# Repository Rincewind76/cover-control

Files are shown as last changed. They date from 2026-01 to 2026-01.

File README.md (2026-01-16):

# Starting Setup
I have the following equipment:
* WandererCover V4-EC Professional Flatpanel
* Celestron EdgeHD 800 with 0.7 reducer and Off-Axis-Guide and a Dew Heater
* ASIAir Plus
* ZWO ASI585MC (main) and ZWO ASI220M (Guide)
* ZWO Autofocuser
* ZWO Filter Wheel
* Sky Watcher EQ6-R Pro

So all equipment can be conviniently controlled by the ASIAir Plus, except the Wanderer Cover...
(To be fair: The Cover can be controlled by a series of power on/off cycles via the ASIAir - but this is a more a pain, than a feature)
I have a small Windows Tablet to control it - but this is overkill, just to open/close the cover and adjust the brightness.

So target of this project is to have a small standalone unit to control everything onsite via local controls (e.g. buttons)

---

# Requirements Collection

- Small controller with Wi-Fi capability to host a web interface
- USB host capability to control the WandererCover via USB virtual COM port  
  - Direct USB connection from the control system to the WandererCover
- Power supply via 12V  
  - The WandererCover is powered and switched through the control system
- Two additional separate 12V outputs, PWM-controlled  
  - For external dew heaters
- Ability to measure voltage level at the 12V input port
- Integrated temperature and humidity sensor
- Separate buttons:
  - Open
  - Close
  - Light on with a selected brightness via Poti
  - Light off
- LED feedback:
  - Light on/off status
  - Wi-Fi connection
  - USB communication feedback
- Optional: OLED support for a 0.96" display  
- Wi-Fi networks configurable via settings  
  - The strongest configured network should be used

---

# Key Components

- Wemos LOLIN S3 Pro
- Brightness adjustable via potentiometer
- BME280 climate sensor via I2C
- OLED AZDelivery SSD1306 0.96" display via I2C
- MOSFET IRLZ44N
- Buck converter 1584EN module

---

# The result - Hardware
I created the schematic and PCB in Kicad.  All files stored in subfolder hardware, there you can also find the gerber files.
Since I am not very good at soldering, therefore the design has only big components, no SMD. To keep it simple, I only wanted a single sided PCB, no Vias, no connections on top layer necessary.
There is only one palce, where sections of the ground plane is connected via the switches - but this seems to be the case in all switches of this form factor.

As I have a Carvera Air desktop CNC, I made the PCB by myself - the results are below

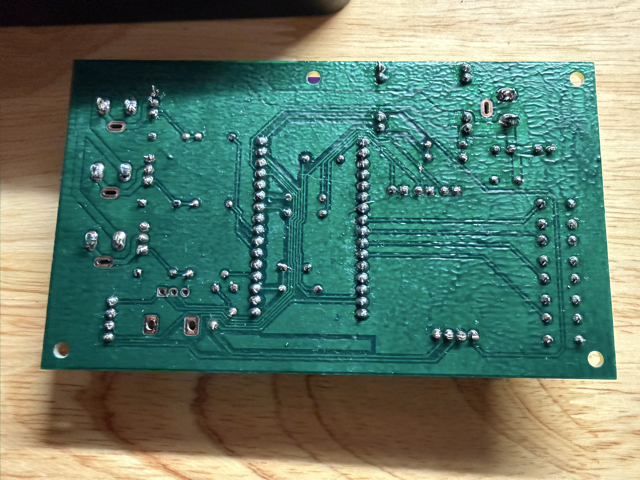
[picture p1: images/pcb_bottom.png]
PCB_Bottom


and the final assembled version looks like this:

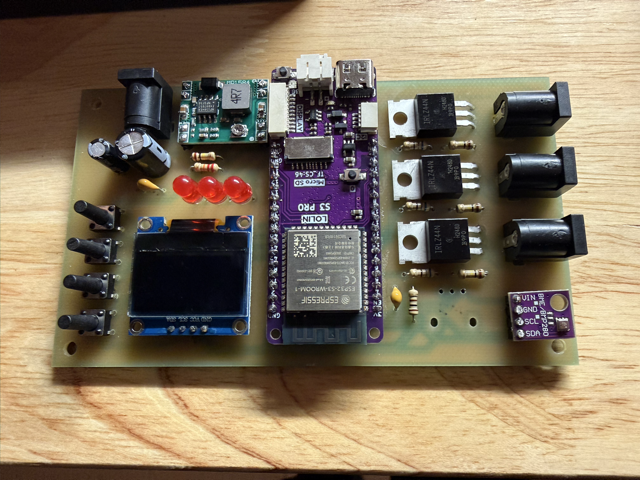
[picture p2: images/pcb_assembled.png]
PCB_Top


After a short check, nothing seems to burn or explode after applying 12V - I went for the next part: software

A small hint: the buck converter is not fixed to 5V - so I recommend to solder that one first, then apply 12V and adjust the poti on the buck converter to get the desired 5V out of it, only then continue with the rest of the components. Otherwise there is the risk to damage components if they see more than the 5V.

# The result - Software
In case you want to adapt the software, just install Visual Studio Code with the PlatformIO extension. The rest gets downloaded automatically if you open the folder in VS Code.
The Lolin S3 Pro has only one USB port - so after the first flashing of the software you cannot use the USB port anymore for updating or logging of events.
All further updates have to be applied via the OTA method, or by manually bringing the ESP32 in the bootloader mode.

The software itself is pretty straight forward. For PIN, WiFi and I2C control you can use standard libraries.

I implemented a scheduler. It gets the time from the internet and can execute certain tasks at a predefined time. Currently I only use it for auto-closing the cover at a certain time in the morning.

First challenge is the serial communication to the cover: Unfortunately I figured out quite late, the the cover uses a CH341 chip - which does not follow the standard CDC communication. Luckily Bert Melis has developed a library to communicate with this chipset. I installed a retry mechanism: after 5s without proper communication it just re-initializes the communication.

The BME280 and OLED display have standard libraries from Adafruit - I just included them.

The Dew heater control is fully automatic, you can specify a maximum rate (usually 70%), then as soon as the temperature goes towards the dew point, the heaters gradually switch on until max power.
Two dew heaters with 12V specification can be attached, in my case I have one for the optics and one at the mount.

The Webserver is based on the ASyncWebserver libraries - quite simple but effective. 

The main page looks like this and can be accessed by http://(-IP of Cover Control-)/ :

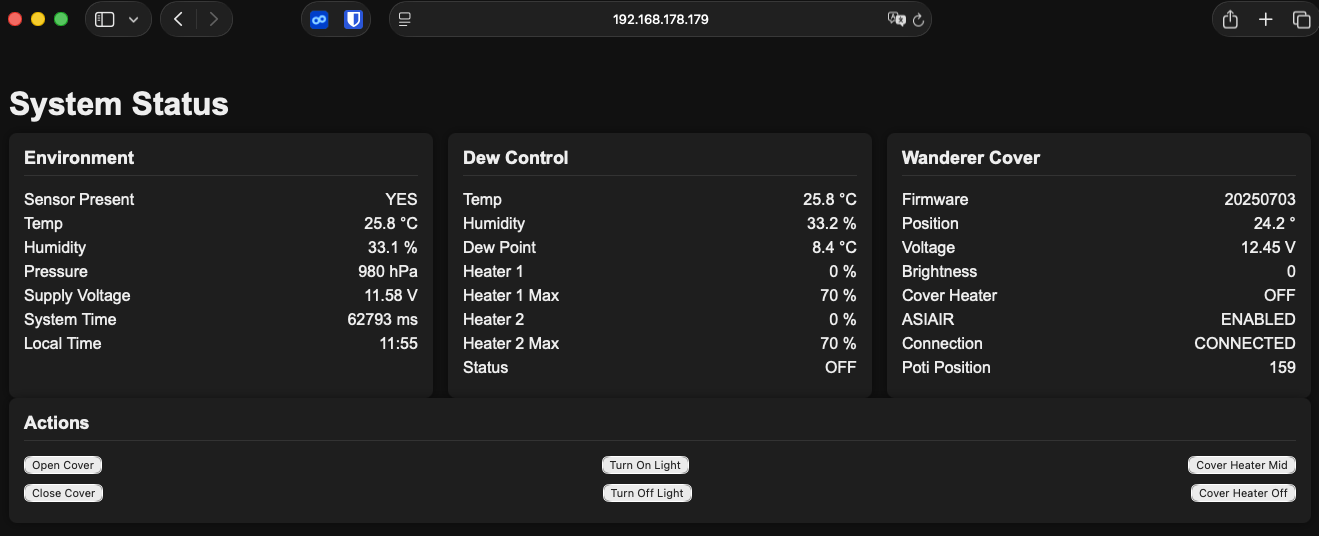
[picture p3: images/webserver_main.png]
Webserver Main


All necessary information is stored there and updated each 2 seconds.

As mentioned before, the logging feature is no longer available via USB due to the communication to the cover, therefore you can access the logged events via the route http://(-IP of Cover Control-)/log

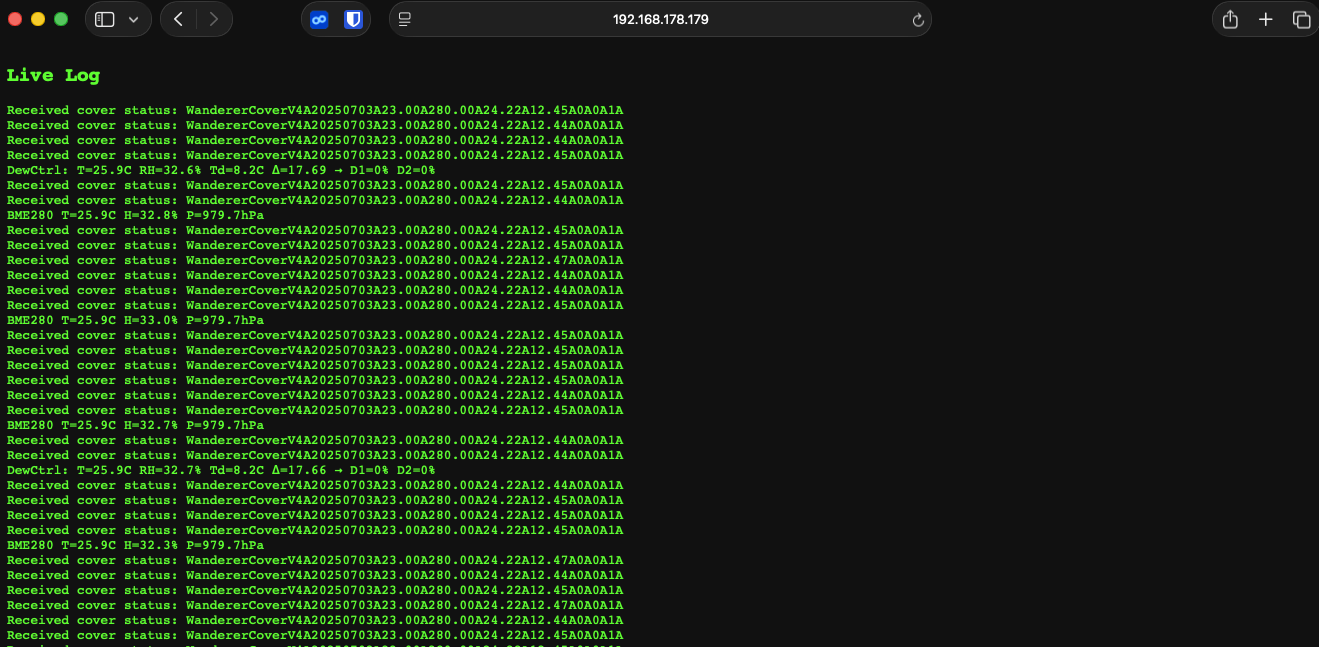
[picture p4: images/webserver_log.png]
Webserver Main


I found it as a pleasant surprise, that the LOLIN S3 Pro has a SD-card reader onboard - so all the configuration is stored in a textfile "config.txt" on the SD-card. The initial version is part of this repository. It can also be updated via Web-Interface - no need to get off the couch ;)

Adress to this page is http://(-IP of Cover Control-)/config

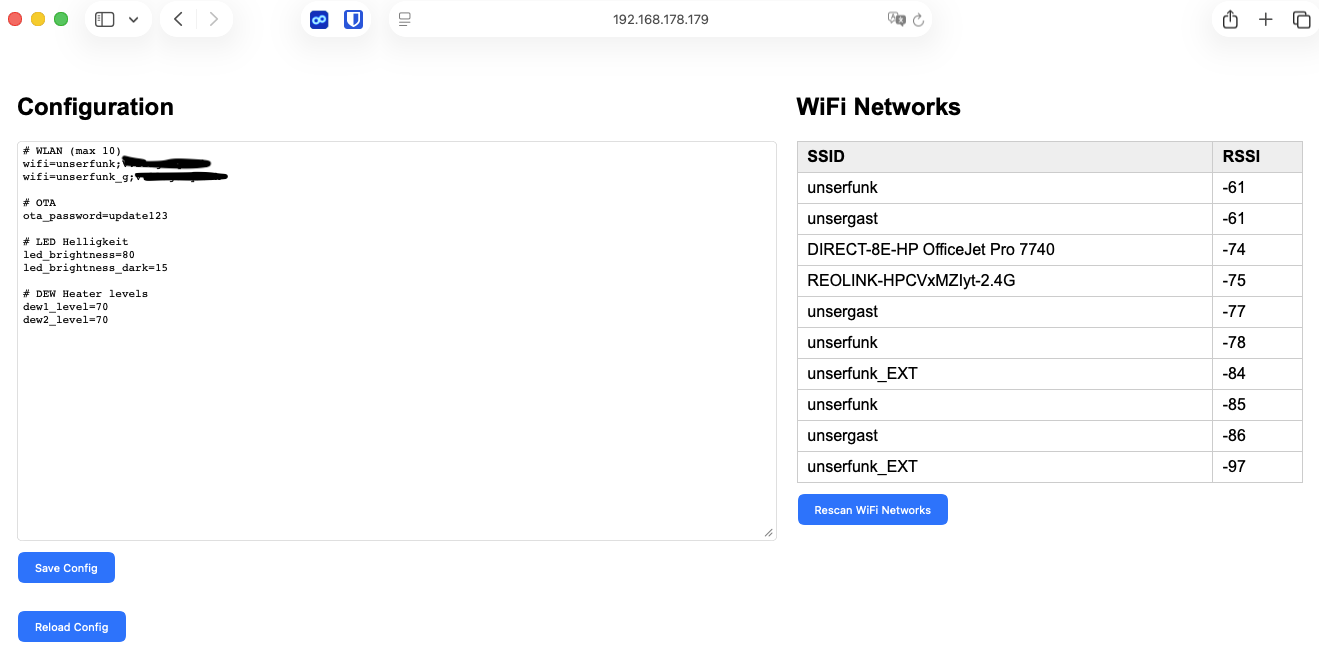
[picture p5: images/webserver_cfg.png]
Webserver Main


As you can see, you can define some basic behaviour - and also access data to WiFi networks (max 10). It automatically selects the strongest network and connects to this - including retry, in case connection gets lost. The format ist quite simple: `wifi=SSID;password` - each wifi network gets a new line. On this page you can also scan for networks to find the strongest one.

The `ota_password=password` is also quite important - this has to match the entry in the platformIO.ini

All in all the software is still below 1MB Flash - so plenty of headroom for more improvements.

# The result - including housing
OK - for the housing my patience was already quite low - so it does not win any beauty prices...

But it is functional - please note, that the temperature sensor is physically separated from the rest of the electronics, so that any heating of components does not affect (too much) the measurement of the surrounding temperature.

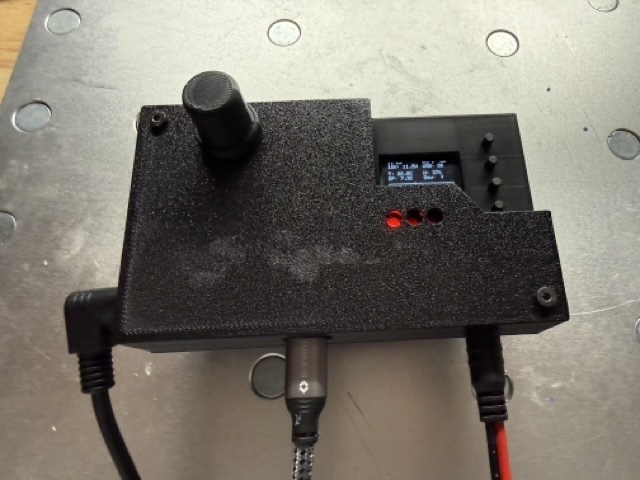
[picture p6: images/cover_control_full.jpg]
Cover Control Housing


The OLED display was initially only a optional feature, but actually I do most of the adjustments with the information provided there:

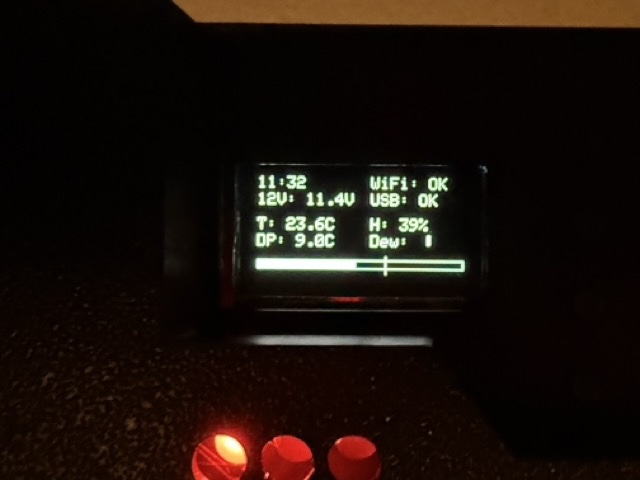
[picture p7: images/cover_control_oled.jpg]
Cover Control OLED


# In the end
I have used this device now for several nights - no problem discovered.

You can freely use this project for your needs (as long as it is non commercial). You have all necessary information here:
- KiCad Project files with schematic and PCB layout
- Exported Gerber Files with bottom layer, top silkscreen, edge cuts and drill files
- CNC files for Makera Carvera Air (or compatible)
- 3MF Files for housing - including the source f3D file for Fusion360
- All Software files incuding platformIO.ini to build the executable

Have fun and clear skies!

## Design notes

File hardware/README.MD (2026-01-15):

# PIN Belegung Lolin S3 Pro:

| PIN | Name | Type | Function |
| --- | ---- | --- | --- |
| GPIO1  | POT_LIGHT  | Analog in | Potentiometer for Light Intensity (50kOhm) |
| GPIO2  | LED_STATUS | Digital Out | Control of Status LED |
| GPIO18 | LED_WLAN | Digital Out | Control of WiFi LED |
| GPIO8  | LED_LIGHT | Digital Out | Control of Light LED |
| GPIO42 | BTN_OPEN | Input Pullup  | Switch input Open Cover, needs software debounce |
| GPIO41 | BTN_CLOSE  | Input Pullup  | Switch input Close Cover, needs software debounce |
| GPIO40 | BTN_LIGHT_ON  | Input Pullup  | Switch input Light on, needs software debounce |
| GPIO39 | BTN_LIGHT_OFF  | Input Pullup  | Switch input Light off, needs software debounce |
| GPIO5  | DEW1_OUT | Digital Out | Enable DEW1 Heater 12V Supply, PWM |
| GPIO7  | DEW2_OUT | Digital Out | Enable DEW2 Heater 12V Supply, PWM |
| GPIO16  | PAN_OUT | Digital Out | Enable Flat Panel 12V Supply |
| GPIO4  | VIN_12V_SENSE  | Analog in | Supply Voltage monitor, voltage divider with 100kOhm and 22kOhm |
| GPIO13  | SD_MISO  | SPI MISO | SPI for SD-Card, MISO |
| GPIO12 | SD_SCK  | SPI CLK | SPI for SD-Card, CLK |
| GPIO11 | SD_MOSI  | SPI MOSI | SPI for SD-Card, MOSI |
| GPIO46 | SD_CS  | SPI CS | SPI for SD-Card, CS |
| GPIO19 | D-  | USB D- | USB Host to Cover, D- |
| GPIO20 | D+  | USB D+ | USB Host to Cover, D+ |
| GPIO9 | SDA  | I2C SDA | I2C bus, connected to BME280 Sensor (0x77) and SSD1306 0,96" OLED Display (0x3C) |
| GPIO10 | SCL  | I2C SCL | I2C bus, connected to BME280 Sensor (0x77) and SSD1306 0,96" OLED Display (0x3C) |

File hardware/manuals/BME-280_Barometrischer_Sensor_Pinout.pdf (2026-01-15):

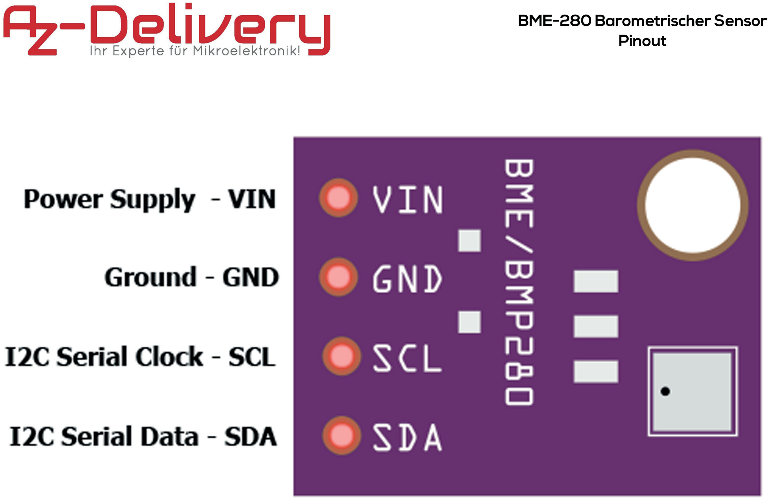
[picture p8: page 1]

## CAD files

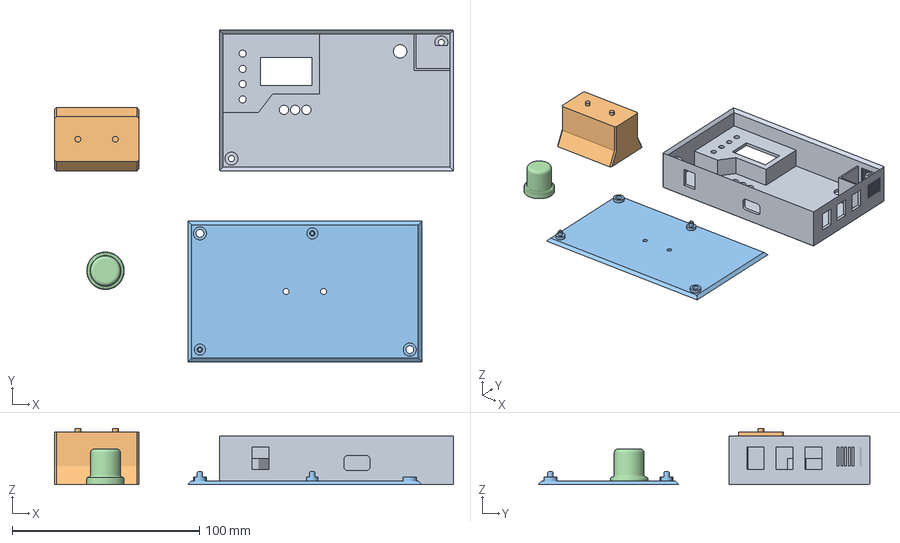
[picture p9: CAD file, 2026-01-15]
hardware/housing/Gehäuse Oben.3mf
212.9 x 176.9 x 30.0 mm
Gehäuse Oben
Haltefuß
Gehäuse Unten
Knopf

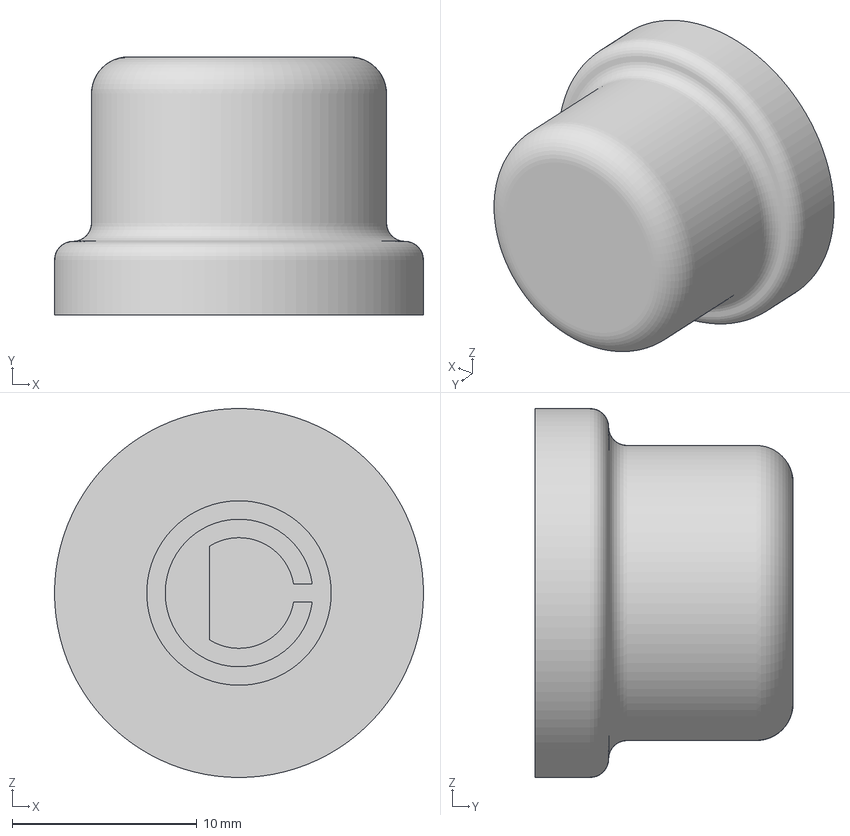
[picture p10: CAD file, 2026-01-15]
hardware/housing/Knopf.3mf
20.0 x 14.0 x 20.0 mm

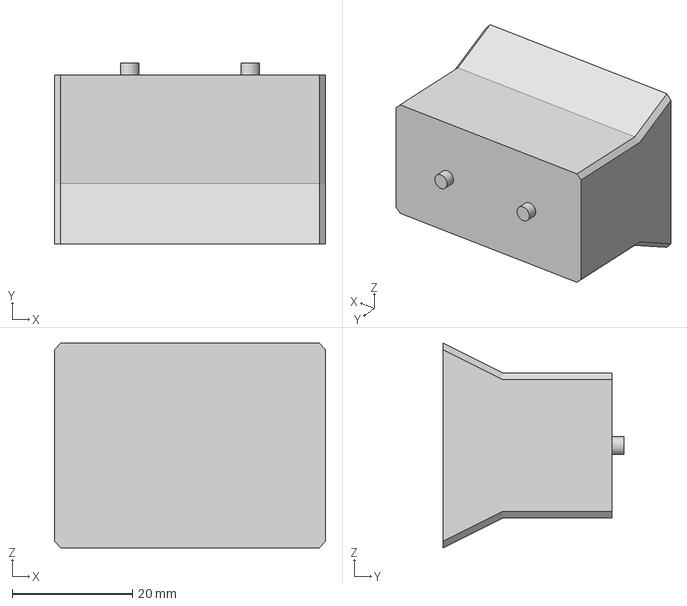
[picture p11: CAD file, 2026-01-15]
hardware/housing/Haltefuß.3mf
45.0 x 30.0 x 34.0 mm

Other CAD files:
hardware/housing/Gehäuse Unten.3mf
hardware/housing/Cover Control Gehäuse.f3d

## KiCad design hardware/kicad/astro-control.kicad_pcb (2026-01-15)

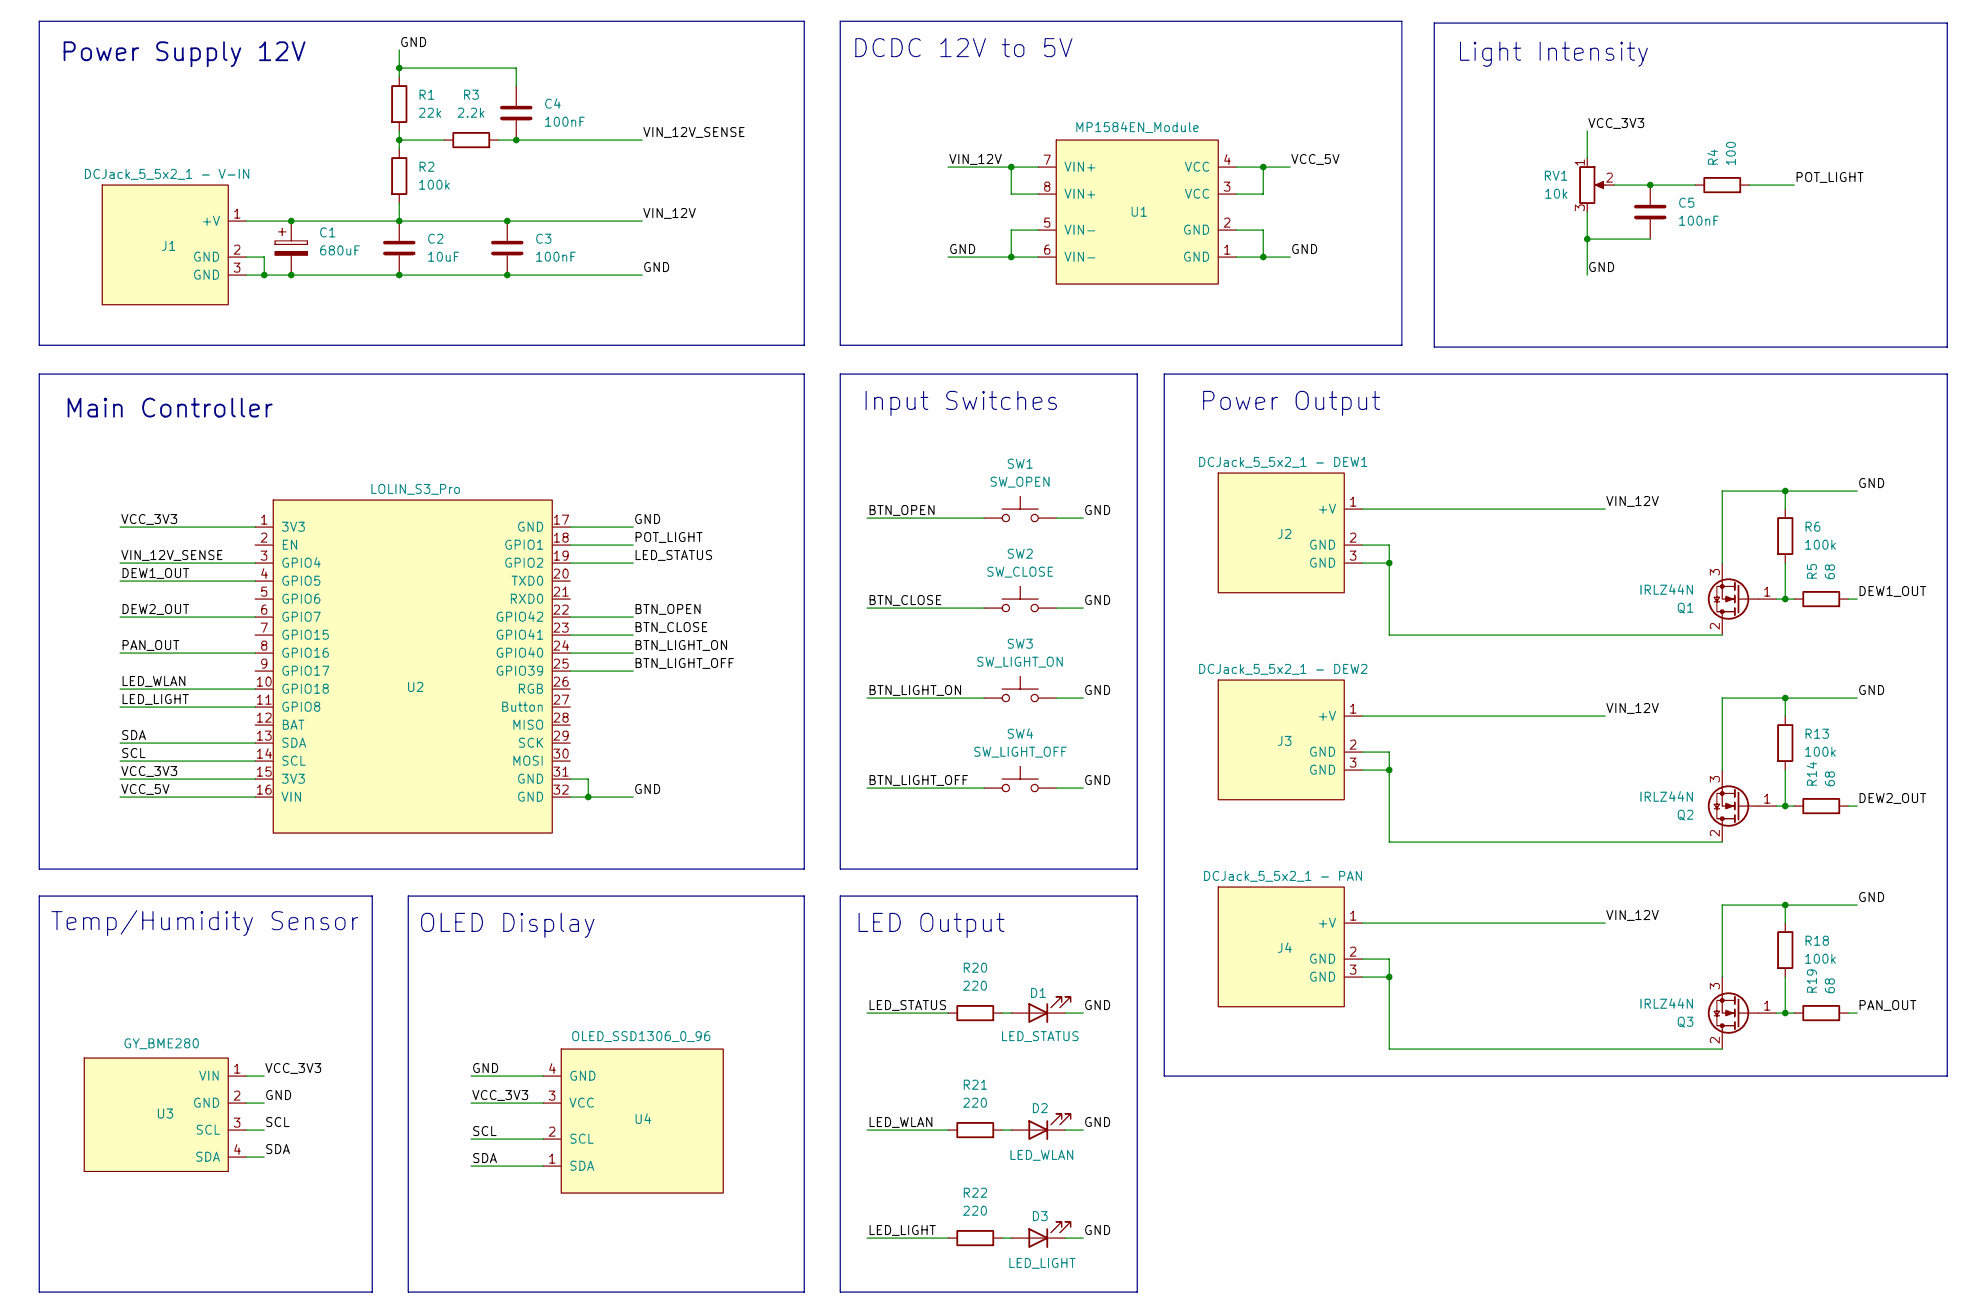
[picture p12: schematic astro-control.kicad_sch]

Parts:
C1: 680uF; CP_Radial_D8.0mm_P3.50mm
C2: 10uF; CP_Radial_Tantal_D5.5mm_P2.50mm
C3, C4, C5: 100nF; C_Disc_D5.1mm_W3.2mm_P5.00mm
D1: LED_STATUS; LED_D3.0mm
D2: LED_WLAN; LED_D3.0mm
D3: LED_LIGHT; LED_D3.0mm
J1: DCJack_5_5x2_1 - V-IN; DCJack_5_5x2_1_Right
J2: DCJack_5_5x2_1 - DEW1; DCJack_5_5x2_1_Right
J3: DCJack_5_5x2_1 - DEW2; DCJack_5_5x2_1_Right
J4: DCJack_5_5x2_1 - PAN; DCJack_5_5x2_1_Right
Q1, Q2, Q3: IRLZ44N; TO-220-3_Vertical
R1: 22k; R_Axial_DIN0207_L6.3mm_D2.5mm_P7.62mm_Horizontal
R2, R6, R13, R18: 100k; R_Axial_DIN0207_L6.3mm_D2.5mm_P7.62mm_Horizontal
R3: 2.2k; R_Axial_DIN0207_L6.3mm_D2.5mm_P7.62mm_Horizontal
R4: 100; R_Axial_DIN0207_L6.3mm_D2.5mm_P7.62mm_Horizontal
R5, R14, R19: 68; R_Axial_DIN0207_L6.3mm_D2.5mm_P7.62mm_Horizontal
R20, R21, R22: 220; R_Axial_DIN0207_L6.3mm_D2.5mm_P7.62mm_Horizontal
RV1: 10k; Potentiometer_Alps_RK09K_Single_Vertical
SW1: SW_OPEN; SW_PUSH_6mm_H5mm
SW2: SW_CLOSE; SW_PUSH_6mm_H5mm
SW3: SW_LIGHT_ON; SW_PUSH_6mm_H5mm
SW4: SW_LIGHT_OFF; SW_PUSH_6mm_H5mm
U1: MP1584EN_Module
U2: LOLIN_S3_Pro; LOLIN_S3_Pro_Module
U3: GY_BME280; GY_BME280_AZ_4P
U4: OLED_SSD1306_0_96; OLED_SSD1306_0v96_I2C_4P

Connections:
/BTN_CLOSE: SW2.1, U2.23 (GPIO41)
/BTN_LIGHT_OFF: SW4.1, U2.25 (GPIO39)
/BTN_LIGHT_ON: SW3.1, U2.24 (GPIO40)
/BTN_OPEN: SW1.1, U2.22 (GPIO42)
/DEW1_OUT: R5.2, U2.4 (GPIO5)
/DEW2_OUT: R14.2, U2.6 (GPIO7)
/GND: C1.2, C2.2, C3.2, C4.1, C5.2, D1.1 (K), D2.1 (K), D3.1 (K), J1.2 (GND), J1.3 (GND), Q1.3 (S), Q2.3 (S), Q3.3 (S), R1.1, R6.1, R13.1, R18.1, RV1.3, SW1.2, SW2.2, SW3.2, SW4.2, U1.1 (GND), U1.2 (GND), U1.5 (VIN-), U1.6 (VIN-), U2.17 (GND), U2.31 (GND), U2.32 (GND), U3.2 (GND), U4.4 (GND)
/LED_LIGHT: R22.1, U2.11 (GPIO8)
/LED_STATUS: R20.1, U2.19 (GPIO2)
/LED_WLAN: R21.1, U2.10 (GPIO18)
/PAN_OUT: R19.2, U2.8 (GPIO16)
/POT_LIGHT: R4.2, U2.18 (GPIO1)
/SCL: U2.14 (SCL), U3.3 (SCL), U4.2 (SCL)
/SDA: U2.13 (SDA), U3.4 (SDA), U4.1 (SDA)
/VCC_3V3: RV1.1, U2.1 (3V3), U2.15 (3V3), U3.1 (VIN), U4.3 (VCC)
/VCC_5V: U1.3 (VCC), U1.4 (VCC), U2.16 (VIN)
/VIN_12V: C1.1, C2.1, C3.1, J1.1 (+V), J2.1 (+V), J3.1 (+V), J4.1 (+V), R2.2, U1.7 (VIN+), U1.8 (VIN+)
/VIN_12V_SENSE: C4.2, R3.2, U2.3 (GPIO4)
unnamed: C5.1, R4.1, RV1.2
unnamed: D1.2 (A), R20.2
unnamed: D2.2 (A), R21.2
unnamed: D3.2 (A), R22.2
unnamed: J2.2 (GND), J2.3 (GND), Q1.2 (D)
unnamed: Q1.1 (G), R5.1, R6.2
unnamed: J3.2 (GND), J3.3 (GND), Q2.2 (D)
unnamed: Q2.1 (G), R13.2, R14.1
unnamed: J4.2 (GND), J4.3 (GND), Q3.2 (D)
unnamed: Q3.1 (G), R18.2, R19.1
unnamed: R1.2, R2.1, R3.1

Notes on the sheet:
DCDC 12V to 5V
Power Output
Light Intensity
OLED Display
Input Switches
LED Output
Power Supply 12V
Temp/Humidity Sensor
Main Controller

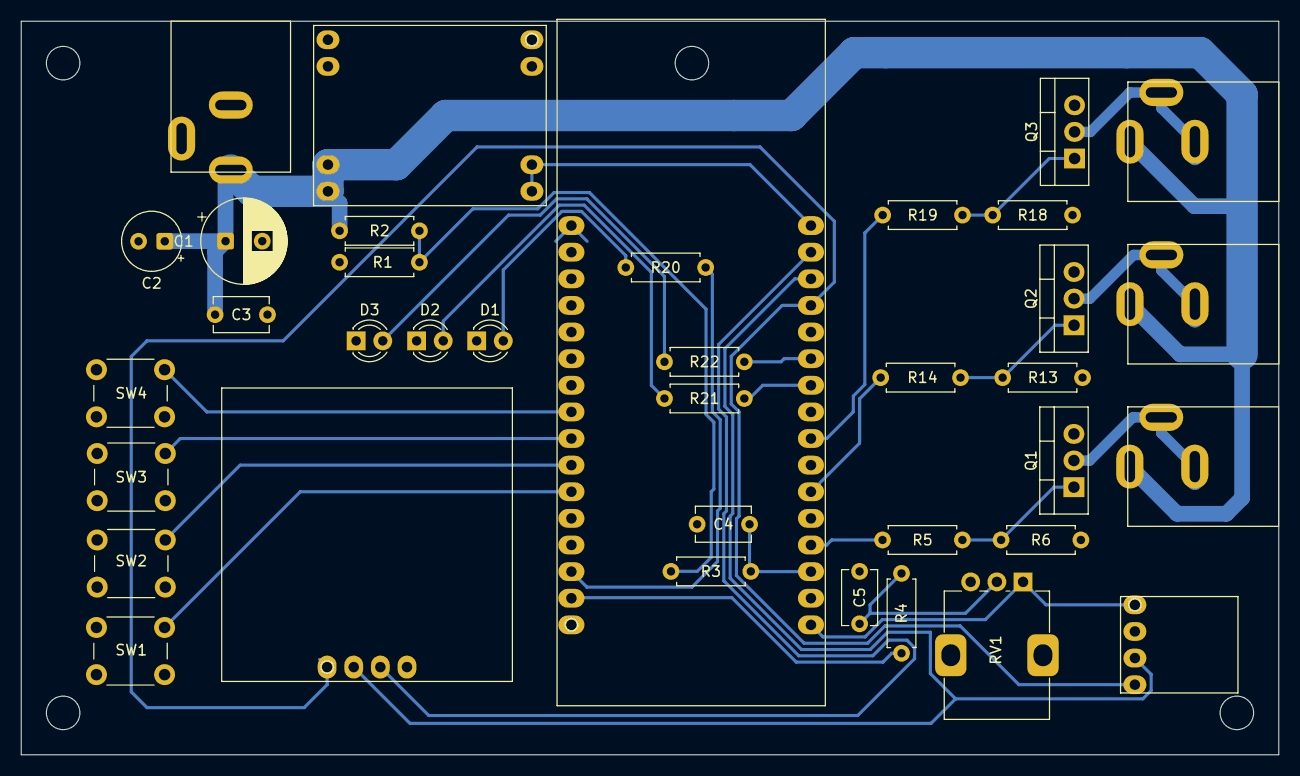
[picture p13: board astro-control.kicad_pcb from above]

Board: 2 copper layers, 120.0 x 70.0 mm, 37 parts (0 on the bottom side), 29 nets.

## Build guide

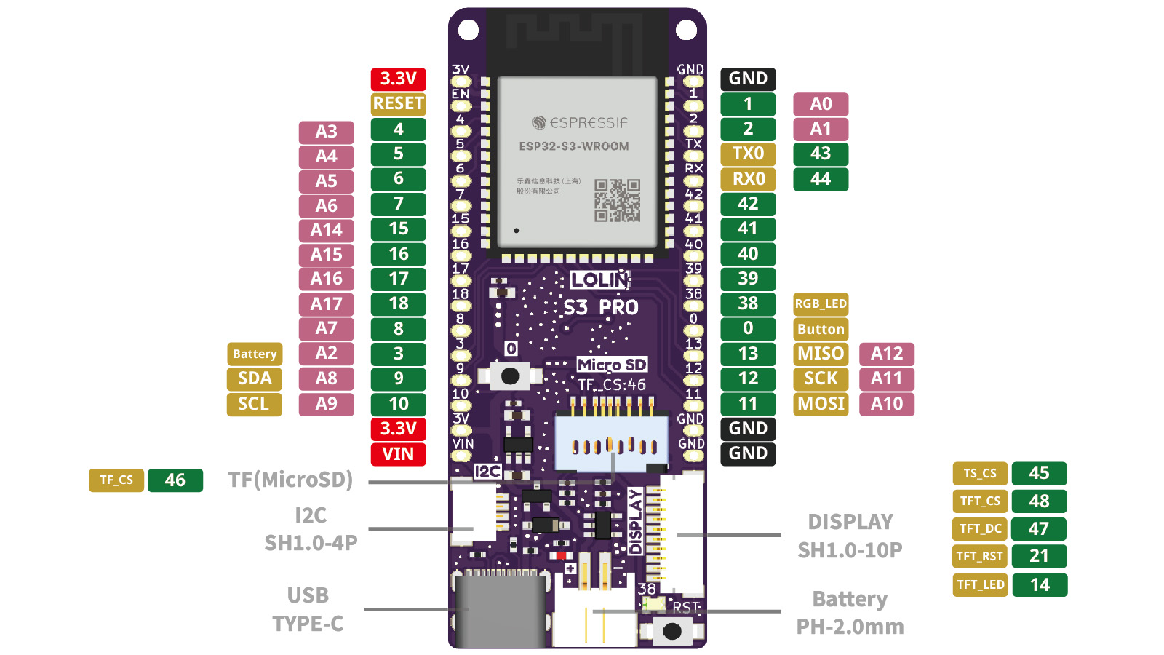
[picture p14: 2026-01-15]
hardware/manuals/s3_pro_v1.0.0_4_16x9.jpg

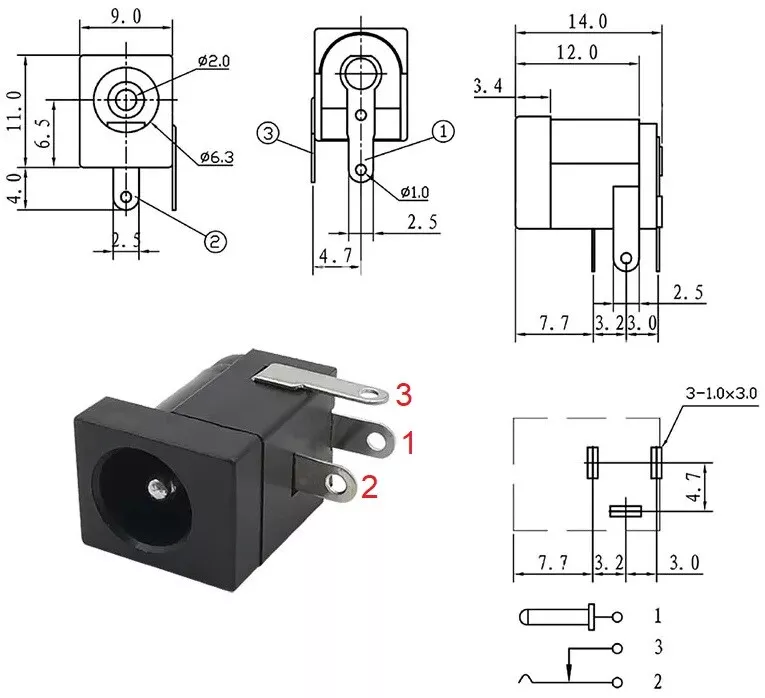
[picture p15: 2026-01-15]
hardware/manuals/dc-jack.webp

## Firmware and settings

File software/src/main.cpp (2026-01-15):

/**
 * @file main.cpp
 * @brief Central setup function and cyclic loop
 *
 * Responsible for:
 * - initialize all subsystems
 * - init order: Pins → SD → Config → WiFi → OTA
 * - cyclic call of non-blocking handler fcunctions

 */

#include <Arduino.h>
#include "pins.h"
#include "sdcard.h"
#include "config_manager.h"
#include "wifi_config.h"
#include "ota.h"
#include "led_manager.h"
#include "button_manager.h"
#include "power_control.h"
#include "webserver.h"
#include "time_manager.h"
#include "web_log.h"
#include "bme280_manager.h"
#include "dew_controller.h"
#include "oled_display.h"
#include "usb_manager.h"

void setup() {

    //Serial.begin(115200);
    //delay(200);

    LOG("+-- Telescope Cover Controller Starting --+");

    initPins();     // GPIO-init
    LOG("Pins initialized");
    initLeds();     // LED initialize
    LOG("LEDs initialized");
    power_init();
    power_setPanel(true); // Power ON flat panel by default
    LOG("Power Outputs initialized");

    initButtons();
    LOG("Buttons initialized");

    // load config from SD card
    if (initSD()) {
        loadConfigFromSD();
    }

    // set LED brightness
    setGlobalLedBrightness(ledBrightnessNormal);

    // Wifi Mode intiialized - NO CONNECTION
    initWiFi();
    delay(100);
    LOG("WiFi initialized");

    // Time Manager init (NTP)
    initTimeManager();
    LOG("Time Manager initialized");

	//Start Webserver
	initWebServer();
    LOG("Webserver started");

    // OTA init after wifi mode initialized
    initOTA();
    LOG("OTA initialized");
    

    // Initialize USB Cover Manager
    //usb_manager_init(); // Initialize USB Host for CH341
    LOG("USB Host initialized");

    // BME280 init
    bme_init();
    dew_init();

    // OLED Display init
    oled_init();

    LOG("End of setup reached");
    LOG("*****************************************************");
}

void loop() {
    handleWiFi();   			// maintain Wifi connections
    handleOTA();    			// OTA-Handler
    updateLeds();   			// LED-Fading
	checkScheduledActions();	// Check for scheduled actions
    updatePoti();               // Update Potentiometer
    updateButtons();            // Update Buttons
    bme_loop();                 // Update BME280 sensor
    dew_update();               // Update Dew Controller
    oled_update();              // Update OLED Display
    usb_manager_update();               // USB Host CH341 task

    //process button events and poti changes
    if (buttonClicked(BTN_OPEN)) { 
        usb_manager_open_cover(); 
        LOG("Button OPEN clicked");
    }
    if (buttonClicked(BTN_CLOSE)) { 
        usb_manager_close_cover(); 
        LOG("Button CLOSE clicked");
    }
    if (buttonClicked(BTN_LIGHT_ON)) { 
        usb_manager_set_brightness(getPotiBrightness()); 
        LOG("Button LIGHT ON clicked");
    }
    if (buttonClicked(BTN_LIGHT_OFF)) { 
        usb_manager_turn_off_light();
        LOG("Button LIGHT OFF clic‚‚ked");
    }
    //handlePotiBrightness();
    
    delay(10);      			// CPU entlasten
}

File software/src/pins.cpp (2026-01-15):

#include "pins.h"

// --- ANALOG INPUTS ---
const uint8_t PIN_POT_LIGHT        = 1;
const uint8_t PIN_VIN_12V_SENSE    = 4;

// --- DIGITAL OUTPUTS ---
const uint8_t PIN_LED_STATUS       = 2;
const uint8_t PIN_LED_WLAN         = 18;
const uint8_t PIN_LED_LIGHT        = 8;

const uint8_t PIN_DEW1_OUT         = 5;
const uint8_t PIN_DEW2_OUT         = 7;
const uint8_t PIN_PAN_OUT          = 16;

// --- BUTTON INPUTS ---
const uint8_t PIN_BTN_OPEN         = 42;
const uint8_t PIN_BTN_CLOSE        = 41;
const uint8_t PIN_BTN_LIGHT_ON     = 40;
const uint8_t PIN_BTN_LIGHT_OFF    = 39;

// --- SD CARD (SPI) ---
const uint8_t PIN_SD_MISO          = 13;
const uint8_t PIN_SD_MOSI          = 11;
const uint8_t PIN_SD_SCK           = 12;
const uint8_t PIN_SD_CS            = 46;

// --- USB HOST ---
const uint8_t PIN_USB_D_MINUS      = 19;
const uint8_t PIN_USB_D_PLUS       = 20;

// --- I2C BUS ---
const uint8_t PIN_I2C_SDA          = 9;
const uint8_t PIN_I2C_SCL          = 10;

// --- INITIALIZATION ---
void initPins() {
    // Digital outputs
    pinMode(PIN_LED_STATUS, OUTPUT);
    pinMode(PIN_LED_WLAN, OUTPUT);
    pinMode(PIN_LED_LIGHT, OUTPUT);

    pinMode(PIN_DEW1_OUT, OUTPUT);
    pinMode(PIN_DEW2_OUT, OUTPUT);
    pinMode(PIN_PAN_OUT, OUTPUT);

    // Buttons (active low)
    pinMode(PIN_BTN_OPEN, INPUT_PULLUP);
    pinMode(PIN_BTN_CLOSE, INPUT_PULLUP);
    pinMode(PIN_BTN_LIGHT_ON, INPUT_PULLUP);
    pinMode(PIN_BTN_LIGHT_OFF, INPUT_PULLUP);

    // Analog inputs → no pinMode() needed

    // SD‑Card pins → handled by SPIClass.begin()

    // USB pins → handled by USB Host stack

    // I2C pins → handled by Wire.begin()

    // Optional: set LEDs off at startup
    digitalWrite(PIN_LED_STATUS, LOW);
    digitalWrite(PIN_LED_WLAN, LOW);
    digitalWrite(PIN_LED_LIGHT, LOW);
}

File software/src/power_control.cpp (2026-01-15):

#include "power_control.h"

/**
 * @brief Initializes all power-related GPIOs and PWM channels.
 */
void power_init()
{
    // --- Supply voltage sense ---
    pinMode(PIN_VIN_12V_SENSE, INPUT);

    // --- PWM for Dew Heater 1 ---
    ledcSetup(PWM_CHANNEL_DEW1, PWM_FREQUENCY, PWM_RESOLUTION);
    ledcAttachPin(PIN_DEW1_OUT, PWM_CHANNEL_DEW1);
    ledcWrite(PWM_CHANNEL_DEW1, 0);

    // --- PWM for Dew Heater 2 ---
    ledcSetup(PWM_CHANNEL_DEW2, PWM_FREQUENCY, PWM_RESOLUTION);
    ledcAttachPin(PIN_DEW2_OUT, PWM_CHANNEL_DEW2);
    ledcWrite(PWM_CHANNEL_DEW2, 0);

    // --- Flat Panel Output ---
    pinMode(PIN_PAN_OUT, OUTPUT);
    digitalWrite(PIN_PAN_OUT, LOW);
}

/**
 * @brief Reads the 12V supply voltage using the analog input.
 */
float power_readSupplyVoltage()
{
    const float dividerFactor = (100000.0f + 22000.0f) / 22000.0f; // 5.545
    const float adcMax = 4095.0f;
    const float vRef = 3.3f;

    int raw = analogRead(PIN_VIN_12V_SENSE);
    return (raw / adcMax) * vRef * dividerFactor;
}

/**
 * @brief Sets the PWM level for Dew Heater 1.
 */
void power_setDew1(int percent)
{
    percent = constrain(percent, 0, 100);
    uint16_t pwm = (percent * ((1 << PWM_RESOLUTION) - 1)) / 100;
    ledcWrite(PWM_CHANNEL_DEW1, pwm);
}

/**
 * @brief Sets the PWM level for Dew Heater 2.
 */
void power_setDew2(int percent)
{
    percent = constrain(percent, 0, 100);
    uint16_t pwm = (percent * ((1 << PWM_RESOLUTION) - 1)) / 100;
    ledcWrite(PWM_CHANNEL_DEW2, pwm);
}

/**
 * @brief Returns the current PWM level of Dew Heater 1.
 */
int power_getDew1Level()
{
    uint32_t raw = ledcRead(PWM_CHANNEL_DEW1);
    int percent = (raw * 100) / ((1 << PWM_RESOLUTION) - 1);
    return constrain(percent, 0, 100);
}

/**
 * @brief Returns the current PWM level of Dew Heater 2.
 */
int power_getDew2Level()
{
    uint32_t raw = ledcRead(PWM_CHANNEL_DEW2);
    int percent = (raw * 100) / ((1 << PWM_RESOLUTION) - 1);
    return constrain(percent, 0, 100);
}

/**
 * @brief Enables or disables the flat panel output.
 */
void power_setPanel(bool on)
{
    digitalWrite(PIN_PAN_OUT, on ? HIGH : LOW);
}

/**
 * @brief Returns the current state of the flat panel output.
 */
bool power_isPanelOn()
{
    return digitalRead(PIN_PAN_OUT) == HIGH;
}

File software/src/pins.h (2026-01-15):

#ifndef PINS_H
#define PINS_H

#include <Arduino.h>

// --- ANALOG INPUTS ---
extern const uint8_t PIN_POT_LIGHT;        // GPIO1
extern const uint8_t PIN_VIN_12V_SENSE;    // GPIO4

// --- DIGITAL OUTPUTS ---
extern const uint8_t PIN_LED_STATUS;       // GPIO2
extern const uint8_t PIN_LED_WLAN;         // GPIO18
extern const uint8_t PIN_LED_LIGHT;        // GPIO8

extern const uint8_t PIN_DEW1_OUT;         // GPIO5 (PWM)
extern const uint8_t PIN_DEW2_OUT;         // GPIO7 (PWM)
extern const uint8_t PIN_PAN_OUT;          // GPIO16

// --- BUTTON INPUTS (active low, pullup) ---
extern const uint8_t PIN_BTN_OPEN;         // GPIO42
extern const uint8_t PIN_BTN_CLOSE;        // GPIO41
extern const uint8_t PIN_BTN_LIGHT_ON;     // GPIO40
extern const uint8_t PIN_BTN_LIGHT_OFF;    // GPIO39

// --- SD CARD (SPI) ---
extern const uint8_t PIN_SD_MISO;          // GPIO13
extern const uint8_t PIN_SD_MOSI;          // GPIO11
extern const uint8_t PIN_SD_SCK;           // GPIO12
extern const uint8_t PIN_SD_CS;            // GPIO46

// --- USB HOST (WandererCover) ---
extern const uint8_t PIN_USB_D_MINUS;      // GPIO19
extern const uint8_t PIN_USB_D_PLUS;       // GPIO20

// --- I2C BUS ---
extern const uint8_t PIN_I2C_SDA;          // GPIO9
extern const uint8_t PIN_I2C_SCL;          // GPIO10

// --- INITIALIZATION ---
void initPins();

#endif

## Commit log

2026-01-15 added kicad files
    [astro-control-B_Cu.gbr, astro-control-B_Mask.gbr, astro-control-Edge_Cuts.gbr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]
2026-01-15 added software
    [partitions_ota.csv, sample_config.txt]
2026-01-15 added housing
    [Cover Control Gehäuse.f3d, Gehäuse Oben.3mf, Gehäuse Unten.3mf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]
2026-01-16 PCB pictures added
2026-01-16 Update README with project requirements and results
    Added requirements and detailed sections for hardware, software, and housing results.
